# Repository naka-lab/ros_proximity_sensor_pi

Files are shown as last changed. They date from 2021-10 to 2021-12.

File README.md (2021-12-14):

# グリッパー用近接覚センサ

## 使用機器
- Raspberry Pi zero
- VL618X x 3

## 配線
| Raspbery Pi | sensor1 | sensor2 | sensor3 |
| --- | --- | --- | --- |
| GPIO21(40番ピン) | VIN  | | | 
| GPIO20(38番ピン) | | VIN  | | 
| GPIO16(36番ピン) | | |  VIN | 
| SCL(5番ピン) | SCL  | SCL  | SCL  | 
| SDA(3番ピン) | SDA  | SDA  | SDA  | 
| GND(6番ピン) | GND  | GND  | GND  | 

- GPIO21, 20, 16は各センサーへの電力供給および，個別にON/OFFするためのスイッチとして利用
- Strethへの取り付けは，[これ](mounter_stretch)を使う

## setup
- Raspberry Piをwifiに接続できるようにする
- ssh, i2cを有効化する
- 依存モジュールインストール：`pip install rospkg catkin_pkg`
- このリポジトリをクローン：`clone https://github.com/naka-lab/ros_proximity_sensor_pi.git`
- 実行するためのシェルスクリプトを作成
   ```
   cp ros_proximity_sensor_pi/start_sensor.sh ./
   chmod +x start_sensor.sh
   nano start_sensor.sh   # シェル内のROS_MASTER_URIとROS_IPを自身の環境に合わせて変更する
   ```
- この時点で`./start_sensor.sh`で実行できることが確認できたらRaspberry Piをリードオンリー化する[[参考]](https://astherier.com/blog/2020/05/change-raspi-to-read-only/#])
  - リードオンリー化後は，Raspberry Piの電源を直接切れるようになります
  - ただしリードオンリー化すると，Rasberry Piへの変更はすべて保存されなため，設定を変えたいときはもとに戻す

## 実行方法
- 正常にセットアップできていれば，sshでRaspberry Piに接続し，シェルクリプト`./start_sensor.sh`を実行するとノードが立ち上がる
- 情報はFloat32MultiArray型のproximity_sensor_valueという名前でpublishされる

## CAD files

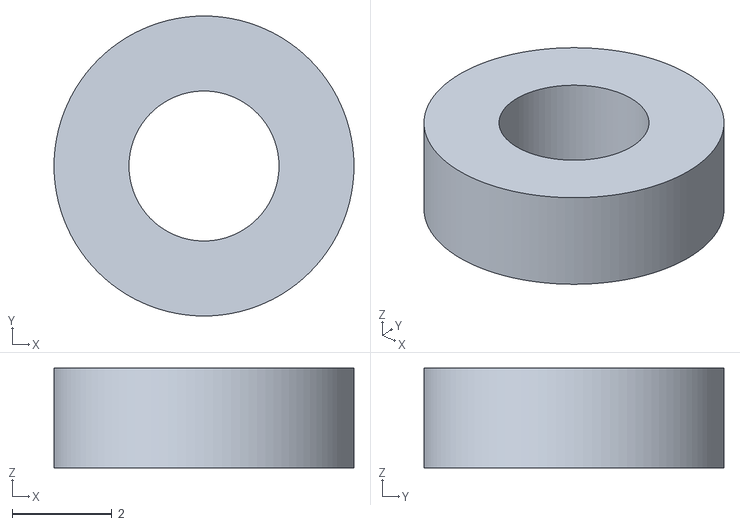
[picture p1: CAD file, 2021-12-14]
mounter_stretch/spacer_2mm.stl
6.00 x 6.00 x 2.00

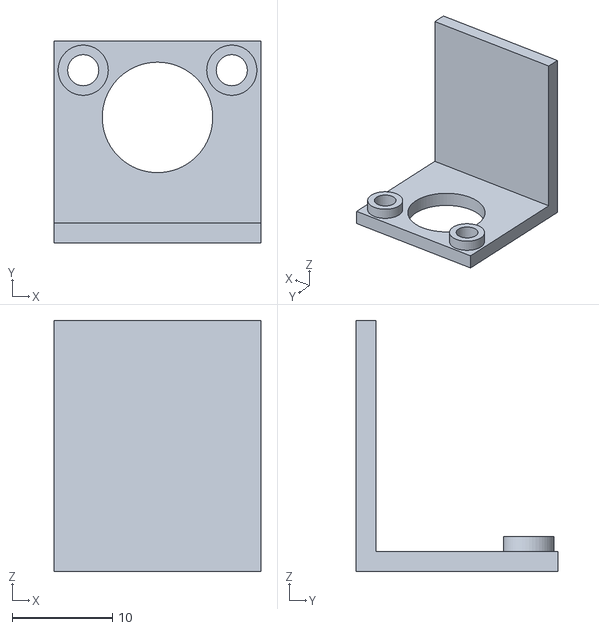
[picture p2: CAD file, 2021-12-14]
mounter_stretch/sensor_mounter.stl
20.6 x 20.1 x 25.0

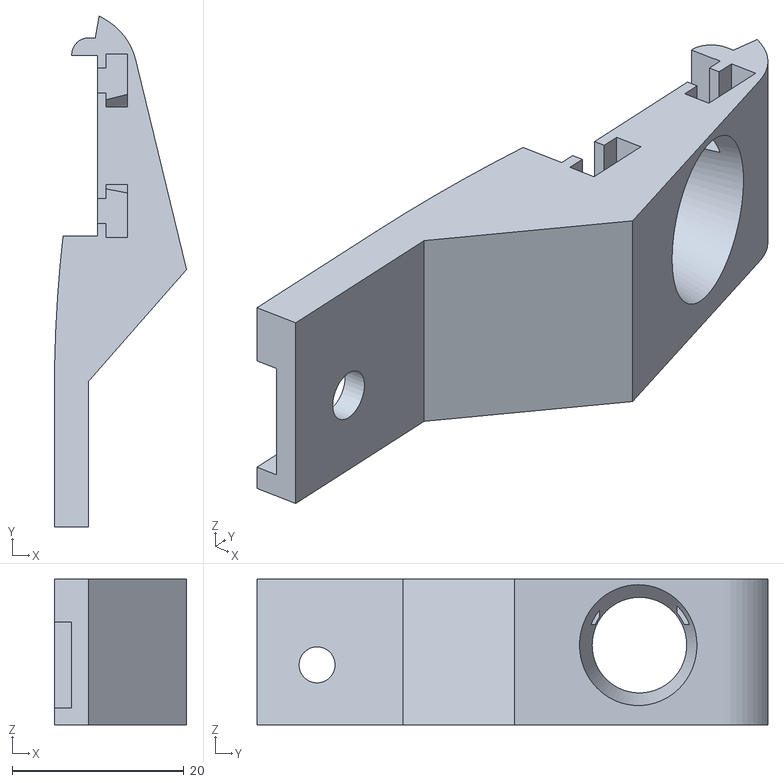
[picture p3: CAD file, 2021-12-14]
mounter_stretch/stretch_finger.stl
15.4 x 59.5 x 17.0

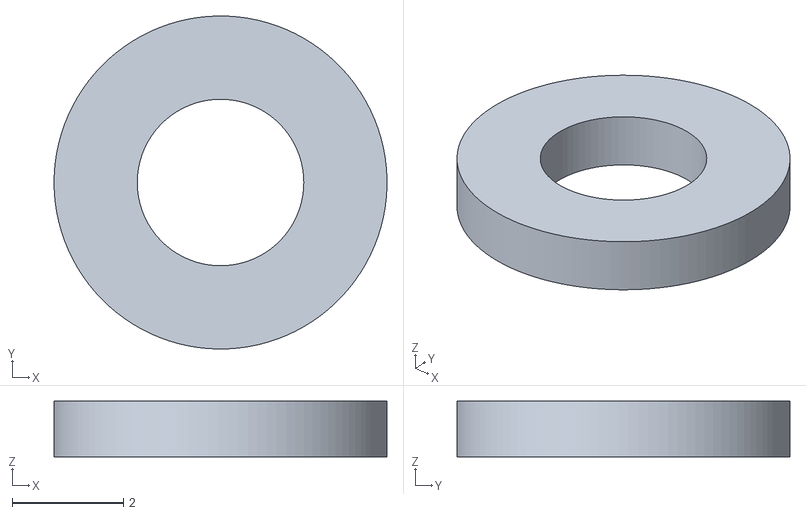
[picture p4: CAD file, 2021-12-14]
mounter_stretch/spacer_1mm.stl
6.00 x 6.00 x 1.00

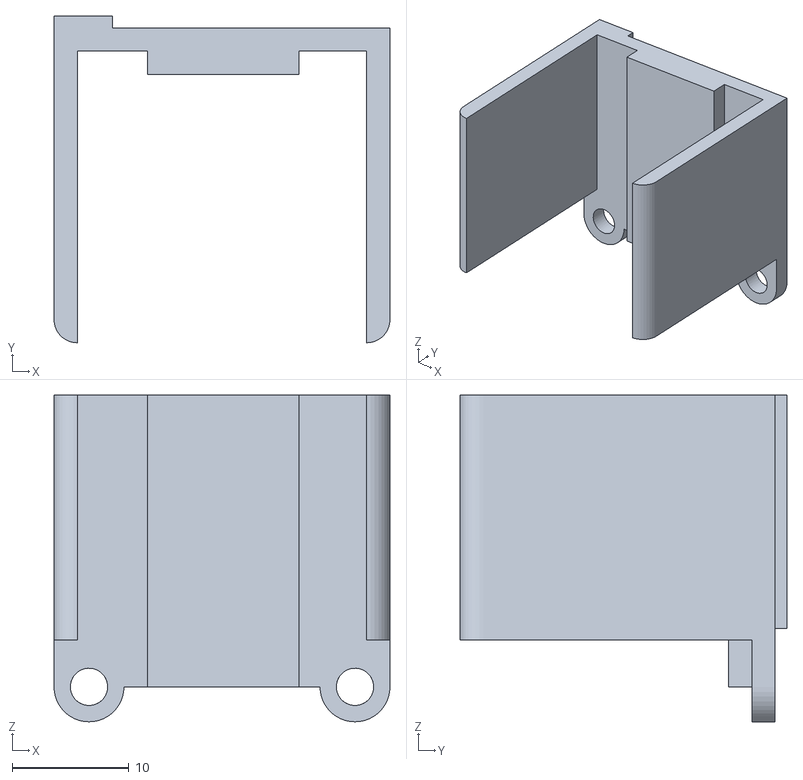
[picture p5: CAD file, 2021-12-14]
mounter_stretch/stretch_raspi_mounter.stl
28.8 x 28.0 x 28.0

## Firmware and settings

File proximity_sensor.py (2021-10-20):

#!/usr/bin/python
# encoding: utf8

import time
import smbus
import RPi.GPIO as GPIO

VL6180X_SYSTEM_FRESH_OUT_OF_RESET = 0x0016
VL6180X_SYSRANGE_MAX_CONVERGENCE_TIME = 0x001C
VL6180X_SYSRANGE_RANGE_CHECK_ENABLES = 0x002D
VL6180X_SYSRANGE_EARLY_CONVERGENCE_ESTIMATE = 0x0022
VL6180X_SYSALS_INTEGRATION_PERIOD = 0x0040
VL6180X_SYSALS_ANALOGUE_GAIN = 0x3F
VL6180X_FIRMWARE_RESULT_SCALER = 0x0120
VL6180X_SYSRANGE_START = 0x0018
VL6180X_RESULT_RANGE_VAL = 0x0062
VL6180X_SYSTEM_INTERRUPT_CLEAR = 0x0015
VL6180X_SYSALS_START = 0x0038
VL6180X_RESULT_ALS_VAL = 0x0050


class ProximitySensor():
    bus = smbus.SMBus(1)

    def __init__(self, addr ):
        self.addr = addr
        self.init_sensor()
    

    def init_sensor(self):
        if self.read(VL6180X_SYSTEM_FRESH_OUT_OF_RESET) == 1:
            print "sensor is ready."
            self.writebyte(0x0207, 0x01)
            self.writebyte(0x0208, 0x01)
            self.writebyte(0x0096, 0x00)
            self.writebyte(0x0097, 0xfd)
            self.writebyte(0x00e3, 0x00)
            self.writebyte(0x00e4, 0x04)
            self.writebyte(0x00e5, 0x02)
            self.writebyte(0x00e6, 0x01)
            self.writebyte(0x00e7, 0x03)
            self.writebyte(0x00f5, 0x02)
            self.writebyte(0x00d9, 0x05)
            self.writebyte(0x00db, 0xce)
     
            self.writebyte(0x00dc, 0x03)
            self.writebyte(0x00dd, 0xf8)
            self.writebyte(0x009f, 0x00)
            self.writebyte(0x00a3, 0x3c)
            self.writebyte(0x00b7, 0x00)
            self.writebyte(0x00bb, 0x3c)
            self.writebyte(0x00b2, 0x09)
            self.writebyte(0x00ca, 0x09)
            self.writebyte(0x0198, 0x01)
            self.writebyte(0x01b0, 0x17)
            self.writebyte(0x01ad, 0x00)
            self.writebyte(0x00ff, 0x05)
            self.writebyte(0x0100, 0x05)
            self.writebyte(0x0199, 0x05)
            self.writebyte(0x01a6, 0x1b)
            self.writebyte(0x01ac, 0x3e)
            self.writebyte(0x01a7, 0x1f)
            self.writebyte(0x0030, 0x00)
        #default_settings
        # Recommended : Public registers - See data sheet for more detail
        self.writebyte(0x0011, 0x10); # Enables polling for 'New Sample ready' when measurement completes
        self.writebyte(0x010a, 0x30); # Set the averaging sample period (compromise between lower noise and increased execution time)
        self.writebyte(0x003f, 0x46); # Sets the light and dark gain (upper nibble). Dark gain should not be changed.
        self.writebyte(0x0031, 0xFF); # sets the # of range measurements after which auto calibration of system is performed
        self.writebyte(0x0040, 0x63); # Set ALS integration time to 100ms DocID026571 Rev 1 25/27 AN4545 SR03 settings27
        self.writebyte(0x002e, 0x01); # perform a single temperature calibration of the ranging sensor
         
        #Optional: Public registers - See data sheet for more detail
        self.writebyte(0x001b, 0x09); # Set default ranging inter-measurement period to 100ms
        self.writebyte(0x003e, 0x31); # Set default ALS inter-measurement period to 500ms
        self.writebyte(0x0014, 0x24); # Configures interrupt on 'New Sample Ready threshold event' 
        self.writebyte(0x016, 0x00); #change fresh out of set status to 0
         
        # Additional settings defaults from community
        self.writebyte(VL6180X_SYSRANGE_MAX_CONVERGENCE_TIME, 0x32)
        self.writebyte(VL6180X_SYSRANGE_RANGE_CHECK_ENABLES, 0x10 | 0x01)
        self.writebyte16(VL6180X_SYSRANGE_EARLY_CONVERGENCE_ESTIMATE, 0x7B)
        self.writebyte16(VL6180X_SYSALS_INTEGRATION_PERIOD, 0x64) #100ms
        self.writebyte(VL6180X_SYSALS_ANALOGUE_GAIN, 0x20) #x40
        self.writebyte(VL6180X_FIRMWARE_RESULT_SCALER, 0x01)

 
 
    def read(self, register16):
        a1 = (register16 >> 8) & 0xFF
        a0 = register16 & 0xFF
        self.bus.write_i2c_block_data(self.addr, a1, [a0])
        return self.bus.read_byte(self.addr)
 
    def read16(self, register16):
        a1 = (register16 >> 8) & 0xFF
        a0 = register16 & 0xFF
        self.bus.write_i2c_block_data(self.addr, a1, [a0])
        data16h = self.bus.read_byte(self.addr)
        data16l = self.bus.read_byte(self.addr)
        return (data16h << 8) | (data16l & 0xFF)
     
    def writebyte(self, register16, data):
        a1 = (register16 >> 8) & 0xFF
        a0 = register16 & 0xFF
        self.bus.write_i2c_block_data(self.addr, a1, [a0, (data & 0xFF)])
     
    def writebyte16(self, register16, data16):
        a1 = (register16 >> 8) & 0xFF
        a0 = register16 & 0xFF
        d1 = (data16 >> 8) & 0xFF
        d0 = data16 & 0xFF
        self.bus.write_i2c_block_data(self.addr, a1, [a0, d1, d0])
     
    def start_scan(self):
        self.writebyte(VL6180X_SYSRANGE_START, 0x03) # continuous mode
        
    def get_distance(self):
        distance = self.read(VL6180X_RESULT_RANGE_VAL)
        self.writebyte(VL6180X_SYSTEM_INTERRUPT_CLEAR, 0x07)
        return distance
        
    def get_light(self):
        self.writebyte(VL6180X_SYSALS_START, 0x01)
        time.sleep(0.5)
        light = self.read16(VL6180X_RESULT_ALS_VAL)
        self.writebyte(VL6180X_SYSTEM_INTERRUPT_CLEAR, 0x07)
        #print read(VL6180X_SYSALS_ANALOGUE_GAIN)
        #print read16(VL6180X_SYSALS_INTEGRATION_PERIOD)
        print light*0.32*100/(32*100),"lux"
        
    def change_address(self, newaddr):
        self.writebyte( 0x212, newaddr )

def turn_on_sensor( gpio, address ):
    GPIO.output(gpio, True)
    time.sleep(1)

    try:
        s = ProximitySensor(0x29)
        s.change_address( address )
        print( "set GPIO21 to adress:%x" % (address) )
    except:
        print("GPI%d is ready. " % (gpio))


def main():
    GPIO.setmode(GPIO.BCM)
    
    # すべて電源をoff
    GPIO.setup(21, GPIO.OUT)
    GPIO.setup(20, GPIO.OUT)
    GPIO.setup(16, GPIO.OUT)
    GPIO.output(21, False)
    GPIO.output(20, False)
    GPIO.output(16, False)
    time.sleep(1)

    # センサーの電源を一つずつonにしてアドレスを設定
    turn_on_sensor( 21, 0x10 )
    turn_on_sensor( 20, 0x11 )
    turn_on_sensor( 16, 0x12 )
    
    """
    # 21番の電源on
    GPIO.setup(21, GPIO.OUT)
    GPIO.output(21, True)
    time.sleep(1)

    try:
        s = ProximitySensor(0x29)
        s.change_address( 0x10 )
        print( "set GPIO21 to adress:0x10" )
    except:
        print("GPIO21 is ready. ")

    # 20番の電源on
    GPIO.setup(20, GPIO.OUT)
    GPIO.output(20, True)
    time.sleep(1)
    
    try:
        s = ProximitySensor(0x29)
        s.change_address( 0x11 )
        print( "set GPIO20 to adress:0x11" )
    except:
        print("GPIO20 is ready. ") 
     """

    s1 = ProximitySensor( 0x10 )
    s2 = ProximitySensor( 0x11 )
    s3 = ProximitySensor( 0x12 )
    s1.start_scan()
    s2.start_scan()
    s3.start_scan()
    while 1:
        d1 = s1.get_distance()
        d2 = s2.get_distance()
        d3 = s3.get_distance()
        print d1, d2, d3

if __name__=="__main__":
    main()

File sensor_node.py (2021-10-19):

#!/usr/bin/env python
# encoding: utf8
from __future__ import print_function, unicode_literals
import rospy
from std_msgs.msg import Float32MultiArray
import os
from proximity_sensor import *
import RPi.GPIO as GPIO

#os.environ["ROS_MASTER_URI"] = "http://192.168.100.10:11311"
#os.environ["ROS_IP"] = "192.168.100.200"

def set_address():
    GPIO.setmode(GPIO.BCM)
    
    # すべて電源をoff
    GPIO.setup(21, GPIO.OUT)
    GPIO.setup(20, GPIO.OUT)
    GPIO.setup(16, GPIO.OUT)
    GPIO.output(21, False)
    GPIO.output(20, False)
    GPIO.output(16, False)
    time.sleep(1)

    # センサーの電源を一つずつonにしてアドレスを設定
    turn_on_sensor( 21, 0x10 )
    turn_on_sensor( 20, 0x11 )
    turn_on_sensor( 16, 0x12 )


def main():
    set_address()

    rospy.init_node('proximity_sensor')
    
    s1 = ProximitySensor( 0x10 )
    s2 = ProximitySensor( 0x11 )
    s3 = ProximitySensor( 0x12 )

    s1.start_scan()
    s2.start_scan()
    s3.start_scan()

    pub = rospy.Publisher('proximity_sensor_value', Float32MultiArray, queue_size=1)
    r = rospy.Rate(10)
    while not rospy.is_shutdown():
        try:
            d1 = s1.get_distance()
            d2 = s2.get_distance()
            d3 = s3.get_distance()
            print( "distance:", d1, d2, d3 )
            pub.publish( Float32MultiArray(data=[d1, d2, d3]) )
            r.sleep()
        except IOError:
            print("IOError")

if __name__ == '__main__':
    main()

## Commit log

2021-10-08 アドレスの自動設定
2021-10-17 キューサイズ変更
2021-10-18 3つ目のセンサーを取り付け
2021-10-19 受信方法変更
2021-12-14 3dモデル追加
    [sensor_mounter.stl, spacer_1mm.stl, spacer_2mm.stl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]
